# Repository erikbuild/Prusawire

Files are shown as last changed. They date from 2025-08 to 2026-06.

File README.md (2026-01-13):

# Prusawire 2025.B1

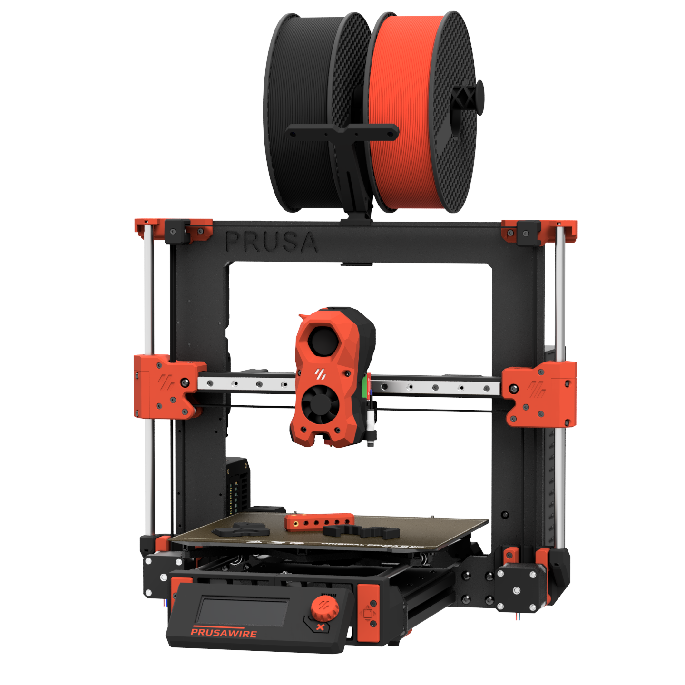
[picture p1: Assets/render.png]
Render


An unofficial Prusa MK3 and MK4 total conversion mod, from Positron's April Fools of 2025.

## Current Release

Beta 1 (2025.B1) was released on 2025-08-21.  There have been [updates and improvements since then](CHANGELOG.md).  Be sure to grab the latest STLs and documentation from the GitHub Repository.

Release 1 (2026.R1) is coming SOON(tm)!

Link to Beta 1 CAD Viewer: [Link](https://positron3d.autodesk360.com/g/shares/SH30dd5QT870c25f12fc28f5f9169dbff2f2)

Link to instructions for gantry de-racking & installing XZ and Y belts: [Link](https://prusawire.positron3d.com/hardware/)

## About

> Nomad of Positron3D came up with this idea shortly after completing their Switchwire build. The idea started as a quick design exercise, to try and convert a Prusa MK4S frame into a Switchwire, using everything left over from a CORE One Upgrade.
>
> As the first iteration wrapped up, I took interest in the project, and decided to take this April Fools joke one step further and build it into a reliable machine.
>
> After months of hard work, please enjoy the build ❤
> 
> -@ellafoxo

## Who This Printer is For

Pick one of the following:

- You have an old MK3, MK3S, or MK3S+, and you want to teach an old dog new tricks and are on a budget
- You upgraded from MK4S to a Core ONE, and have a leftover frame. You are okay spending money on building a new printer with that hardware.

Additionally, the following says this printer is for you: 

- You want to take your first steps into RepRap beyond Prusa, and Voron is an exciting route.
- You are comfortable working from a CAD file as your build guide
- You respect the Frankenstein-y nature of this April Fools joke printer

## Want to Support the Project?

First of all, thank you! Development costs have been mostly self-funded, with filament sponsored by Levendigs, and LDO Motors for providing the funds for the Prusa MK4 frame.

- Support Positron3D to fund future endeavors: 
   - [Donate to Positron3D](https://www.paypal.com/donate/?hosted_button_id=YGPRVTSHN4FQG)
   - [Positron3D Merch](https://nomadsgalaxy-shop.fourthwall.com/)

## Build Volume

X: 250mm
Y: 210mm
Z: 185mm

## Bill of Materials

[Prusawire 2025.B1 Bill of Materials](BOM/BOM_2025-B1.md)

## Technical Support

Prusawire, technically, does not count as a Voron Switchwire. We ask you kindly not to nag the Voron Design team for technical support.

Instead, please [join the Positron3D Discord](https://discord.gg/positron) for support with your build, and maybe share your progress over there too.

## Serial Numbers

We are accepting serials over on the [Positron 3D Discord](https://discord.gg/positron). Please submit your request to the #prusawire-serial-request channel over there. 

## Upgrading the Einsy Rambo to Klipper - Read this

Installing Klipper on the Einsy Rambo board is possible, with extra steps. Follow the guide [published by the awesome folks at MyRigs3D](https://myrigs3d.com/blogs/infos/revive-your-prusa-mk3s-with-klipper-1-5-flash-bootloader)! We recommend Method 2.

**Note:** Some users have reported problems using `avrdude` with the latest Raspberry Pi OS version (bookworm). If you experience error messages from avrdude complaining about gpio ports being busy, please try using the bullseye version of Raspberry Pi OS instead, available as "Raspberry Pi OS (Legacy)" in Raspberry Pi Imager.

## Klipper Configuration Files

The most up–to–date Klipper configuration files for setting up or updating the Prusawire are in our [config repository](https://github.com/Positron3D/prusawire-klipper-config).

## Credits 

Many thanks to all the awesome people and companies that have made this possible. Notably:

Most importantly:
- Ella Fox, _the architect of Beta 1_ - who took Prusawire from a joke to a beautiful and powerful machine. [Buy Ella a Ko-Fi](https://ko-fi.com/ellafoxo)

And also:
- Prusa Research - Cheers, Josef and the team for the MK3/4 platform on which this was built upon!
- Voron Design - Switchwire

- Positron 3D Team - Too many to name, you know who you are <3
- Early development team:
   - Nomad's Galaxy
   - Koosh
   - Birb
- Jason @ LDO Motors - Part sponsorship
- Levendigs - Part sponsorship 
- Early access testers:-
   - Killa_Prints
   - LinksLab
   - Safe
   - Silicon
   - TheNexusAvenger
   - torsten
- Contributors since Beta 1
   - einarjh
   - erikbuild

## Extra Credits for Existing Printed Parts

See the collection for the most up to date! To name them:

- Printable M3 T-Nuts for 3030 Extrusion, by Kapplion
- Stealthburner umbilical strain relief, by nagelwerkstatt

## Team

Prusawire is currently maintained by the Positron 3D Team.

- Design Lead: @Safe-ty
- Documentation Lead: @erikbuild
- Software Lead: @TheNexusAvenger

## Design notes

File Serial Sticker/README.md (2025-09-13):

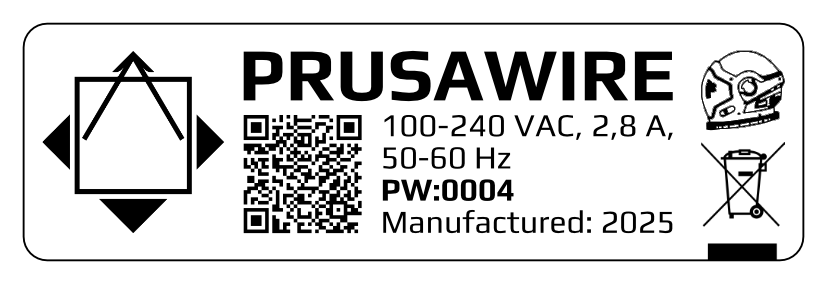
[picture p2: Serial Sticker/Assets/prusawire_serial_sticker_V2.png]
Prusawire Serial


Custom serial sticker for Prusawire. Designed for 24 mm tape. Files include a printable cutting stencil.

Template files are available as Affinity Designer 2 and Inkscape files.
Used fonts are from [Google Fonts](https://fonts.google.com/specimen/Play). Play in regular and bold.

[Inkscape](https://inkscape.org)

[WEEE symbol](https://europa.eu/youreurope/business/product-requirements/labels-markings/weee-label/index_en.htm)

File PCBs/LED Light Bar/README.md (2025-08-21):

# Prusawire Daylight Stick by Ella Fox

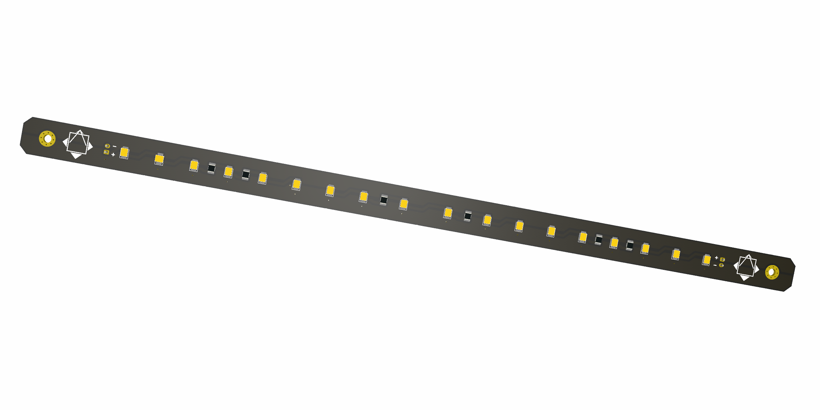
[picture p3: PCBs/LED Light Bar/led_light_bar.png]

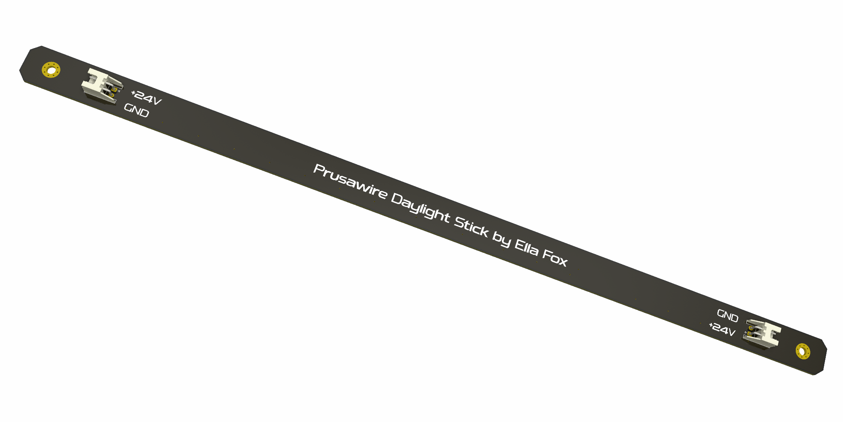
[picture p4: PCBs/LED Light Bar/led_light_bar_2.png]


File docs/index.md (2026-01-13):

---
layout: default
title: Home
nav_order: 1
---

# Positron3D's Prusawire Documentation



An unofficial Prusa MK3 and MK4 to Switchwire total conversion mod, from Positron 3D's April Fools of 2025.

## Current Release

Beta 1 (2025.B1) was released on 2025-08-21.  There have been updates and improvements since then.  Be sure to grab the latest STLs and documentation from the GitHub Repository.

Beta 2 is coming SOON(tm).

## About

> Nomad of Positron3D came up with this idea shortly after completing their Switchwire build. The idea started as a quick design exercise, to try and convert a Prusa MK4S frame into a Switchwire, using everything left over from a CORE One Upgrade.
>
> As the first iteration wrapped up, I took interest in the project, and decided to take this April Fools joke one step further and build it into a reliable machine.
>
> After months of hard work, please enjoy the build ❤
> 
> -@ellafoxo

## Who This Printer is For

Pick one of the following:

- You have an old MK3, MK3S, or MK3S+, and you want to teach an old dog new tricks and are on a budget
- You upgraded from MK4S to a Core ONE, and have a leftover frame. You are okay spending money on building a new printer with that hardware.

Additionally, the following says this printer is for you: 

- You want to take your first steps into RepRap beyond Prusa, and Voron is an exciting route.

## Technical Support

Prusawire, technically, does not count as a Voron Switchwire. We ask you kindly not to nag the Voron Design team for technical support.

Instead, please [join the Positron3D Discord](https://discord.gg/positron) for support with your build, and maybe share your progress over there too.

## Serial Numbers

We are accepting serials over on the [Positron 3D Discord](https://discord.gg/positron). Please submit your request to the #prusawire-serial-request channel over there. 

## Want to Support the Project?

First of all, thank you! Development costs have been mostly self-funded, with filament sponsored by Levendigs, and LDO Motors for providing the funds for the Prusa MK4 frame.

- Support Positron3D to fund future endeavors: 
    - [Donate to Positron3D](https://www.paypal.com/donate/?hosted_button_id=YGPRVTSHN4FQG)
    - [Positron3D Merch](https://nomadsgalaxy-shop.fourthwall.com/)

## Credits 

Many thanks to all the awesome people and companies that have made this possible.

Most importantly:
- Ella Fox, _the architect of Beta 1_ - who took Prusawire from a joke to a beautiful and powerful machine. [Buy Ella a Ko-Fi](https://ko-fi.com/ellafoxo)

And also:
- Prusa Research - Cheers, Josef and the team for the MK3/4 platform on which this was built upon!
- Voron Design - Switchwire
- Positron 3D Team - Too many to name, you know who you are <3
- Early development team:
    - Nomad's Galaxy
    - Koosh
    - Birb
- Jason @ LDO Motors - Part sponsorship
- Levendigs - Part sponsorship 
- Early access testers:
    - Killa_Prints
    - LinksLab
    - Safe
    - Silicon
    - TheNexusAvenger
    - torsten
- Contributors since Beta 1
    - einarjh
    - erikbuild

## Team

Prusawire is currently maintained by the Positron 3D Team.

- Design Lead: @Safe-ty
- Documentation Lead: @erikbuild
- Software Lead: @TheNexusAvenger

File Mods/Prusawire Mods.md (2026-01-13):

# Prusawire Mods

*This is a non-exhaustive collection of Prusawire Mods. Many of these were created for Beta 1.*

## Electronics
- [Prusawire MMU LCD Cover with insert letters by @einarjh](https://www.printables.com/model/1392274-prusawire-mmu-lcd-cover-with-inset-letters)
- [BTT PI TFT50 V2.1 Prusawire Housing by @telefaksi](https://www.printables.com/model/1384689-btt-pi-tft50-v21-prusawire-housing)
- [Prusawire BigTreeTech HDMI 5 Mount by @TheNexusAvenger](https://www.printables.com/model/1377302-prusawire-bigtreetech-hdmi-5-mount)
- [Prusawire ELectronics Tower (w/ xBuddy Box) by @TheNexusAvenger](https://www.printables.com/model/1415732-prusawire-electronics-tower)
- [Prusawire Electronics Tower (w/ all printed parts) by @WaschBaer](https://www.printables.com/model/1464165-skr-mini-e3-v3-printable-case-pi3b-backplate-mods)

## Wiring
- [Prusawire Cable Management Mods by @telefaksi](https://www.printables.com/model/1374187-prusawire-cable-management-mods)
- [Prusawire Cable Management - Additional Mods by @erikbuild](https://www.printables.com/model/1422355-prusawire-cable-management-additional-mods)

## Power Supplies
- [Meanwell LRS-350 / RSP-320 PSU Mount by @erikbuild](https://www.printables.com/model/1386144-meanwell-lrs-350-24-rsp-320-24-psu-mount-for-prusa)

## Decking / Panels
- [Prusawire Deck Panel for Countersunk Screws by @Safe](https://www.printables.com/model/1374282-prusawire-deck-panel-for-countersunk-screws)
- [Prusawire Beta 1 - Rear Deck Cover Plate by @erikbuild](https://www.printables.com/model/1384528-prusawire-rear-deck-cover-plate)

## Frame and Motion
- [Prusawire Key-Bak Mounting Bracket by @telefaksi](https://www.printables.com/model/1371269-prusawire-key-bak-mounting-bracket)
- [TPU Feet for Prusawire and Voron V0 (Alternative to purchased rubber feet!)](https://www.printables.com/model/1442105-tpu-feet-for-prusawire-and-voron-v0)
- [PZ Probe Mount for Prusawire Stealthburner Carriage by @Jarhead](https://www.printables.com/model/1368943-pz-probe-mount-for-prusawire-beta-1)

## Aesthetics
- [Prusawire Supplemental Badge by @TheNexusAvenger](https://www.printables.com/model/1368495-prusawire-supplemental-badge)

## Major Mods
- [XZ Belt Reroute (Under the printer instead of over) by @WaschBaer](https://www.printables.com/model/1466188-beltreroute-better-center-of-mass-more-z-height)

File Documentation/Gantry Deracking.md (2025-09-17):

# Prusawire Gantry Deracking

*This procedure is a composite of initial advice from @ellafoxo, @thenomad, and @safe from the Positron Discord.*

**Current Compatibility:** *Prusawire - Beta 1*

## Overview
The gantry de-racking procedure is critical to ensure smooth motion in X and Z.  The general idea is to loosen certain screws on the gantry, bump the bottom of the gantry against the X and Z motor joints to align, and tighten the screws.

## Prerequisites
- Confirm your frame geometry is square: [Frame Assembly - Geometry Check| Prusa Knowledge Base](https://help.prusa3d.com/guide/2-frame-assembly_427481#427929)
- The following should be assembled already:
	- Frame
	- Z-Axis
	- X-Gantry with toolhead mount
- You should be ready to belt both the X and Z axis.

## Instructions
1. Remove the **toolhead** from the **carriage mount** (if currently installed).
	1. For Stealthburner, see the Stealthburner assembly manual for instructions.
2. Remove the **bed**, **y-carriage**, and **y-rods** completely off the printer (if currently installed).
3. Remove the **bumper block** and **door puller block** from the back of the gantry (if currently installed).

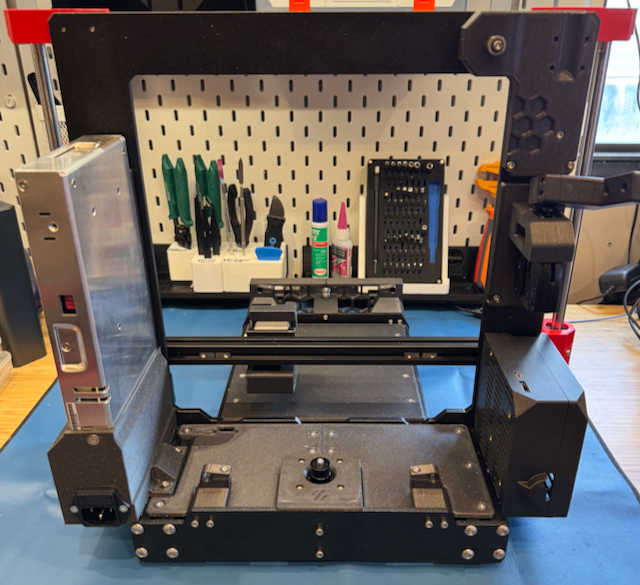
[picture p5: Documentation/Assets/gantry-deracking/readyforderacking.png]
Prusawire ready for deracking.
  	

4. Remove the **top left idler assembly** and **top right idler assembly** loosening the M3 SHCS on each.  
	1. *TIP: A small piece of tape on the top and bottom of the assembly can be used to help keep the bearing stack together.*

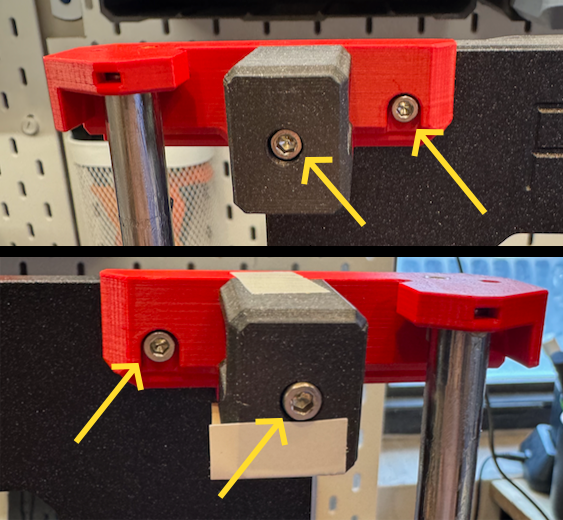
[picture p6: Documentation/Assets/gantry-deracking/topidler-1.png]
Top idlers showing screw locations for removal.
    
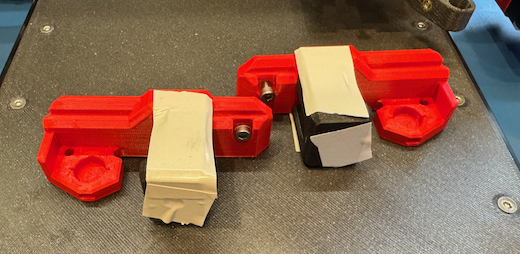
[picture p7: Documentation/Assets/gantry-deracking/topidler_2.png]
Top idles removed and held together with tape.
    

5. Remove the **x-gantry assembly from the printer** by lifting it up off the z-axis rods.
6. Loosen all six **M5 BHCS** from each side of the x-gantry assembly.

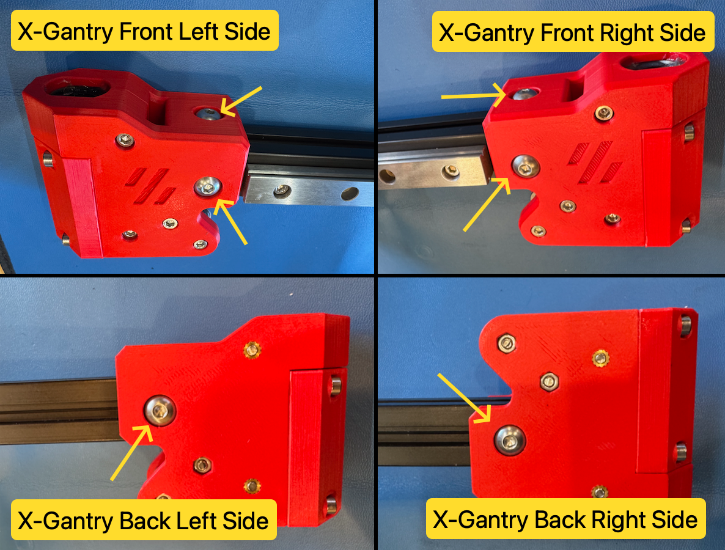
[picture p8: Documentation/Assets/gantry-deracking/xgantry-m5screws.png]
Location of M5 SHCS for adjusting gantry extrusion.
    

7. Ensure each end of the 2020 extrusion is seated ALL the way into the printed parts.
8. Re-install the **x-gantry assembly** onto the printer by sliding it onto the z-axis rods from the top.
9. Move the **x-gantry assembly** up and down a few times to allow parts to settle.
10. Lower the **x-gantry assembly** until it bumps against the X and Z motor mounts.

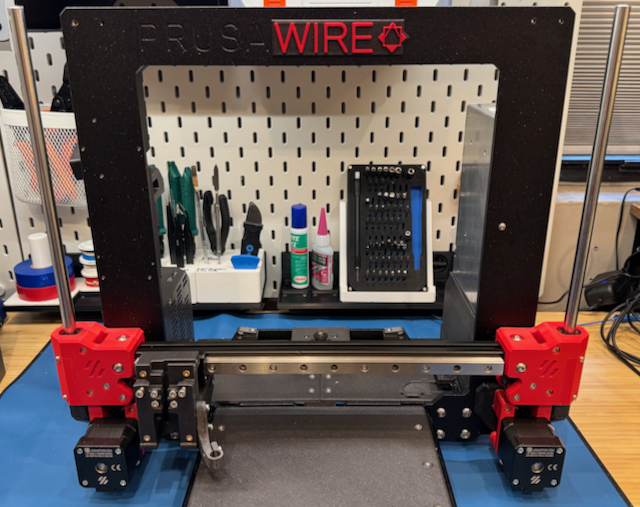
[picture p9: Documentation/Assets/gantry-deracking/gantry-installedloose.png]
Gantry resting on motor mounts.
	

11. Tighten the two top M5 BHCS on the x-gantry assembly, followed by the two front M5 BHCS.

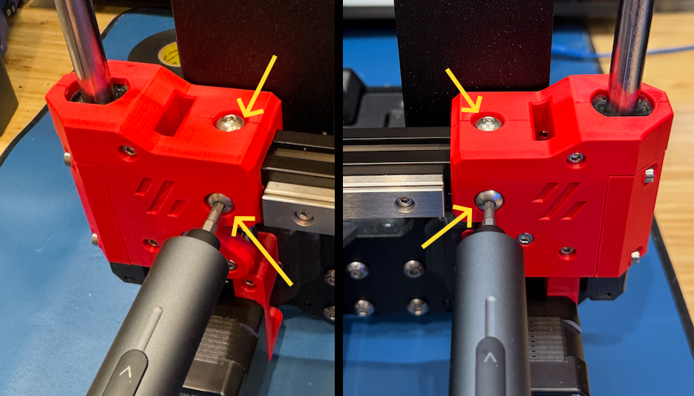
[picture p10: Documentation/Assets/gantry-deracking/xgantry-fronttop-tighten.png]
Image showing M5 BHCS locations.
    

12. Raise the **x-gantry assembly** up to the top just high enough to be able to tighten the rear two M5 BHCS.

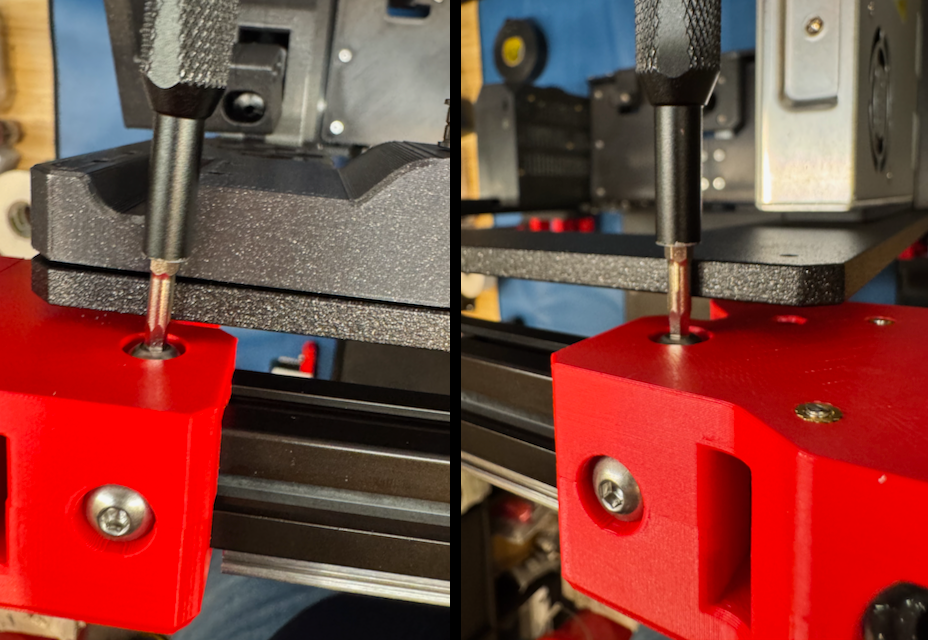
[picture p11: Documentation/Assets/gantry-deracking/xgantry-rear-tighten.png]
Image showing rear M5 BHCS locations on back of gantry.
    

13. Lower the **x-gantry assembly** back down to the bottom.
14. Re-install the **top left idler assembly** and **top right idler assembly** by tightening the two M3 SHCS on each.
15. Re-install the **bumper block** and **door puller block** on the rear of the gantry.
16. Move the gantry up and down.  You shouldn't feel any resistance.

	GIF showing smooth gantry movement and no play.

	1. When the gantry bumps the top of the frame, it should bump equally on both sides.

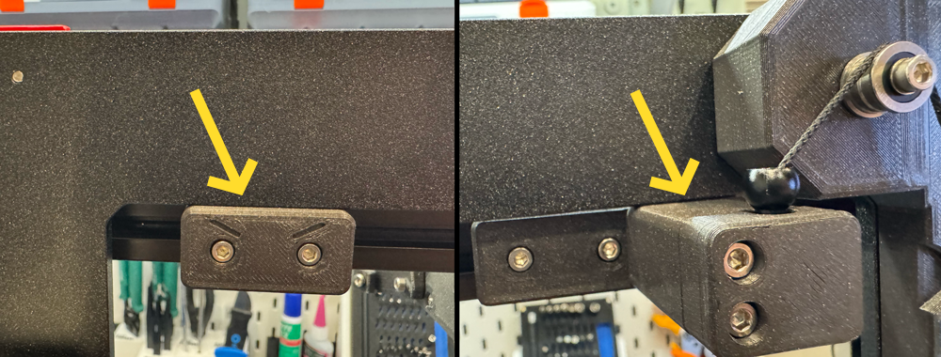
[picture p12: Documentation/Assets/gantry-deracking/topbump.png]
Image showing no gap between bump stop and frame.
    

	2. When the gantry bumps the bottom (X motor mount and Z motor mount), it should bump equally on both sides.

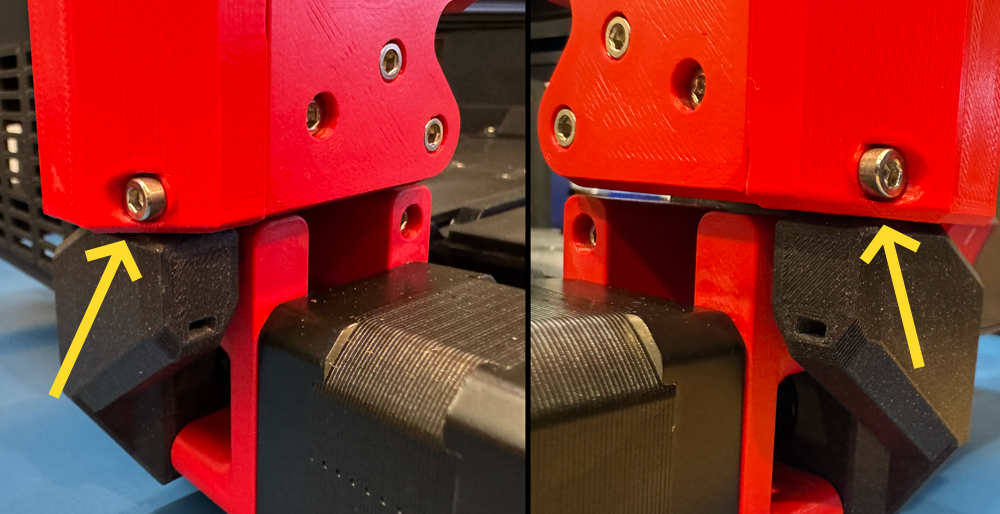
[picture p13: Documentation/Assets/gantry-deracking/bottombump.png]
Image showing no gap between gantry and motor mounts.
    

17. Check for any gantry racking a final time after installing XZ belts (and prior to installation of Y-axis).  Adjust front/top M5 screws if needed.

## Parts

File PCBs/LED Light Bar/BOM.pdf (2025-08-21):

### LED Light Bar

### Page 1

ID | Designator | Footprint | Quantity | Designation Supplier and ref
1 | LED_PLCC_2835_Handsoldering | 18 | LED
2 | R5,R1,R2,R3,R4,R6 | R_1210_3225Metric_Pad1.30x2.65mm_HandSolder | 6 | 100R 0.5W
3 | J1,J2 | JST_XH_S2B-XH-A_1x02_P2.50mm_Horizontal | 2 | Power

D4,D12,D9,D2,D11,D14,D16,D15,D3,
D10,D18,D6,D1,D17,D13,D8,D7,D5

Cree JB2835AWT-W-U40GA0000-N0000001

Digikey: 2138-JB2835AWT-W-U40GA0000-N0000001DKR-ND (https://www.digikey.com/en/products/detail/cree-led/JB2835AWT-W-U40GA0000-N0000001/10820192)

Yageo RC1210JR-07100RL

Digikey: 13-RC1210JR-07100RLDKR-ND (https://www.digikey.com/en/products/detail/yageo/RC1210JR-07100RL/5919841)

JST S2B-XH-A

Digikey: 455-S2B-XH-A-ND (https://www.digikey.com/en/products/detail/jst-sales-america-inc/S2B-XH-A/1651055)

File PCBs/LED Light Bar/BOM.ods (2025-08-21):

ID | Designator | Footprint | Quantity | Designation | Supplier and ref
1 | D4,D12,D9,D2,D11,D14,D16,D15,D3,D10,D18,D6,D1,D17,D13,D8,D7,D5 | LED_PLCC_2835_Handsoldering | 18 | LED | Cree JB2835AWT-W-U40GA0000-N0000001 Digikey: 2138-JB2835AWT-W-U40GA0000-N0000001DKR-ND (https://www.digikey.com/en/products/detail/cree-led/JB2835AWT-W-U40GA0000-N0000001/10820192)
2 | R5,R1,R2,R3,R4,R6 | R_1210_3225Metric_Pad1.30x2.65mm_HandSolder | 6 | 100R 0.5W | Yageo RC1210JR-07100RL Digikey: 13-RC1210JR-07100RLDKR-ND (https://www.digikey.com/en/products/detail/yageo/RC1210JR-07100RL/5919841)
3 | J1,J2 | JST_XH_S2B-XH-A_1x02_P2.50mm_Horizontal | 2 | Power | JST S2B-XH-A Digikey: 455-S2B-XH-A-ND (https://www.digikey.com/en/products/detail/jst-sales-america-inc/S2B-XH-A/1651055)

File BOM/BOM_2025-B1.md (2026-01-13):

# Prusawire 2025.B1 Bill of Materials

This Bill of Materials is accurate for Prusawire version 2025.B1

## Hardware Kit Sources
[KB-3D: BOM Hardware / Fastener Kit - Prusawire - Beta 1](https://kb-3d.com/store/configurators/5743-bom-hardware-fastener-kit-prusawire-beta-1-1755965660392.html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) (affiliate link)

[West3D: Prusawire Stainless Steel Fastener Kit (BDF)](https://collabs.shop/d4usq3) (affiliate link)

| Category | Component | Standard | Optional? | Qty | Notes | Alternative Source 1 | Alternative Source 2 | Alternative Source 3 | Alternative Source 4 |
| --- | --- | --- | --- | --- | --- | --- | --- | --- | --- |
| **Filament** | Primary Color (Black) | PC, ASA, ABS | | 1 | Recommended a carbon or glass filled material to prevent warpage on larger parts. If you cannot print this, then bed adhesive and patience with PC, ABS, or ASA are advised. | [Prusament PC Blend CF (Prusa)](https://www.prusa3d.com/product/prusament-pc-blend-carbon-fiber-black-800g-6)<br>[Affiliate Link](https://www.prusa3d.com/product/prusament-pc-blend-carbon-fiber-black-800g-6/#a_aid=nomad&a_bid=e2885a92) | [FormFutura Kratos PC CF10](https://formfutura.com/product/kratos-pc-cf/)<br><br>[USA (Fabreeko) ASA](https://www.fabreeko.com/products/3do-black-asa-fillament) | [LDO ASA-CF (EU)](https://levendigs.com/collections/filament/products/ldo-asa-cf-filament-1-75mm-1kg-black) | [3DO ASA (EU)](https://3do.dk/en/asa/502-3do-asa-1kg-black.html) |
| | Secondary Color (Red) | | | 1 | | [Prusament ASA (Prusa)](https://www.prusa3d.com/product/prusament-asa-lipstick-red-850g/)<br>[Affiliate Link](https://www.prusa3d.com/product/prusament-asa-lipstick-red-850g/#a_aid=nomad&a_bid=e2885a92) | [Polymaker PolyLite ABS](https://us.polymaker.com/products/polylite-abs?variant=39574342664249) | [LDO ASA (EU)](https://levendigs.com/products/ldo-abs-filament-1-75mm-1kg-red) | [3DO ASA (EU)](https://3do.dk/en/asa/501-814-3do-asa-1kg-red.html#/32-colour-red) |
| **Printed Parts** | Printed Parts | | | 1 | | Print it yourself | Ask a friend | Ask the Positron Discord | |
| **Fasteners** | M5x30 BHCS | ISO 7380 | | 2 | Buy extra fasteners, always! | | | | |
| | M5x16 BHCS | ISO 7380 | | 32  | | | | | |
| | M5x10 BHCS | ISO 7380 | | 4 | | | | | |
| | M5x8 BHCS | ISO 7380 | | 2 | | | | | |
| | M5 Hex Nut | DIN 934 | | 2 | | | | | |
| | M5 T-Nut for 2020 Extrusion | | | 6 | | | | | |
| | M4x10 BHCS | ISO 7380 | | 2 | | | | | |
| | M3x40 SHCS | ISO 4762 / DIN 912 | | 7 | | | | | |
| | M3x30 SHCS | ISO 4762 / DIN 912 | | 22  | Bolt Depot | KB-3D or West3D | Bolt Depot | 3DKatten or TME (EU) | |
| | M3x25 SHCS | ISO 4762 / DIN 912 | | 10  | | | | | |
| | M3x20 SHCS | ISO 4762 / DIN 912 | | 14  | | | | | |
| | M3x16 SHCS | ISO 4762 / DIN 912 | | 7 | | | | | |
| | M3x14 SHCS | ISO 4762 / DIN 912 | | 5 | | | | | |
| | M3x12 SHCS | ISO 4762 / DIN 912 | | 11  | | | | | |
| | M3x10 SHCS | ISO 4762 / DIN 912 | | 82  | | | | | |
| | M3x8 SHCS | ISO 4762 / DIN 912 | | 15  | | | | | |
| | M3x10 BHCS | ISO 7380 | | 11  | Low profile bed cable mount | | | | |
| | M3x30 BHCS | ISO 7380 | | 1 | Used for the Y idler bearing stack. **FYI: 2025 Beta 1 hardware kits from KB-3D and West3D may not yet include this!** | | | | |
| | M3x8 BHCS | ISO 7380 | | 3 | | | | | |
| | M3x6 BHCS | ISO 7380 | Yes | 9 | Used for the newer bed expansion joints. Optional if you use the classic MK3 spacers. | | | | |
| | M3x4 FHCS | ISO 10642 | Yes | 8 | | | | | |
| | M3x16 FHCS | ISO 10642 | Yes | 1 | Used for the MK52 bed in the center. Optional if you use the classic MK3 spacers. | | | | |
| | M3 Shim Washer 3x6x0.5mm | DIN 988 | | 35  | Absolutely do not use normal washers. These must be shim washers built to higher tolerances. | [KB-3D](https://kb-3d.com/store/inserts-fasteners-adhesives/287-3x6x05mm-shim-ring-washer-pack-of-50-din988-1634423217623.html)<br>[Affiliate Link](https://kb-3d.com/store/inserts-fasteners-adhesives/287-3x6x05mm-shim-ring-washer-pack-of-50-din988-1634423217623.html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) | [Replimat Labs (EU)](https://www.replimat.eu/3x6x0.5mm-shim-ring-din-988-40-pcs/rt10079) | [TME (EU)](https://www.tme.eu/de/en/details/b3_6_0.5_bn1976/washers/bossard/1225340/) | [TME (USA)](https://www.tme.com/us/en-us/details/b3_6_0.5_bn1976/washers/bossard/1225340/) |
| | M3 Nylon Lock Nut | DIN 985 | Yes | 7 | 1x needed for y_idler_block. The rest are for Older MK3 Y carriage (if you have the newer MK4 Y carriage, 6x can be eliminated.) | | | | |
| | M3 Hex Nut | DIN 934 | | 10  | 1x needed for y_idler_block. | | | | |
| | M3 Square Nut | DIN 562 | | 14  | Prusa-style M3 Square Nut (Slim) is ideal, but V0 Square Nuts now work! | | | | |
| | M3 Threaded Insert - M3x5x4 (Voron spec) | | | 100 | Buy extra! | [CNC Kitchen (EU)](https://cnckitchen.store/products/made-for-voron-gewindeeinsatz-threaded-insert-m3x5x4-100-stk-pcs) | [Vector3D (UK)](https://vector3d.shop/products/heat-set-insert-m3-voron) | | |
| | M3 T-Nut for 3030 Extrusion | | Yes | 28  | This can be really annoying to source, so we included a printable version instead which uses a heat set insert. Getting the metal ones is totally optional. | [Prusa](https://www.prusa3d.com/product/psu-holder-m3ne-2/)<br>[Affiliate Link](https://www.prusa3d.com/product/psu-holder-m3ne-2/#a_aid=nomad&a_bid=e2885a92) | [KB-3D](https://kb-3d.com/store/extrusion-framing/245-t-nut-roll-in-30-series-8mm-slot-width-m3-threads-1657989315930.html)<br>[[Affiliate Link]](https://kb-3d.com/store/extrusion-framing/245-t-nut-roll-in-30-series-8mm-slot-width-m3-threads-1657989315930.html) | | |
| | M3 T-Nut for 2020 Extrusion | | | 10  | | | | | |
| | M2x10 Self-Tapping Screw for Plastics | | | 4 | Raspberry Pi mounting | | | | |
| **Motion** | GATES GT2 Open Belt LL-2GT-6 (6mm wide) - 1600mm | | | 2 | Genuine GATES belts are required for every open loop belt on the machine. Don't bother with the clones. | [KB-3D](https://kb-3d.com/store/motion/215-gates-powergrip-2gt-belt-open-6mm-width.html)<br>[Affiliate Link](https://kb-3d.com/store/motion/215-gates-powergrip-2gt-belt-open-6mm-width.html?affp=22155) | [West3D](https://west3d.com/products/gates-gt2-open-belt-ll-2gt-6-6mm-wide-voron-v0-v1-v2-switchwire)<br>[Affiliate Link](https://west3d.com/products/gates-gt2-open-belt-ll-2gt-6-6mm-wide-voron-v0-v1-v2-switchwire?dt_id=524416) | [3DKatten (EU)](https://3dkatten.se/products/gates-power-grip-gt-ll-2gt-epdm-balte-1-meter?variant=48182522741059) | |
| | GATES GT2 Open Belt LL-2GT-6 (6mm wide) - 1000mm | | | 1 | [Levendigs (EU)](https://levendigs.com/products/gates-2gt-belt-1cm) | | | | |
| | GT2 20T (6mm wide) Pulley (5mm bore) | | | 3 | | [KB-3D](https://kb-3d.com/store/motion/213-gates-powergrip-2gt-pulley-20-tooth-5mm-6mm-1634481851944.html)<br>[Affiliate Link](https://kb-3d.com/store/motion/213-gates-powergrip-2gt-pulley-20-tooth-5mm-6mm-1634481851944.html?affp=22155) | [West3D](https://west3d.com/products/black-pulleys-and-idlers-gt2-20t-gt2-16t?variant=42151451525332)<br>[Affiliate Link](https://west3d.com/products/black-pulleys-and-idlers-gt2-20t-gt2-16t?variant=42151451525332&dt_id=524416) | [3DKatten (EU)](https://3dkatten.se/products/20t-2gt-5mm-id-pulley?variant=48182169600323) | |
| | F623-2RS Bearing | | | 20  | Don't cheap out here. Use quality bearings for smooth printer operation and longevity. | [KB-3D](https://kb-3d.com/store/magnets-bearings/168-3x10x4-flanged-metric-ball-bearing-f623-2rs-6440891415288.html)<br>[Affiliate Link](https://kb-3d.com/store/magnets-bearings/168-3x10x4-flanged-metric-ball-bearing-f623-2rs-6440891415288.html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) | [West3D](https://west3d.com/products/f623-2rs-flange-ball-bearing)<br>[Affiliate Link](https://west3d.com/products/f623-2rs-flange-ball-bearing?dt_id=524416) | [Replimat (EU [DE])](https://www.replimat.eu/fushi-f623-2rs-abec-7/rt10209) | [AliExpress (Rain & Dew)](https://www.aliexpress.com/item/1005008564381498.html) |
| | Linear Rail MGN12H (300mm), Z1 preload | | | 1 | Z1 preload recommended | [KB-3D](https://kb-3d.com/store/motion/377-5160-kb3d-mgn12h-linear-rail-guide-with-carriage-multiple-lengths-1646161437836.html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)<br>[Affiliate Link](https://kb-3d.com/store/motion/377-5160-kb3d-mgn12h-linear-rail-guide-with-carriage-multiple-lengths-1646161437836.html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) | [West3D](https://west3d.com/products/west3d-printing-mgn12h-1r-300-350-400-linear-rails-with-carriages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)<br>[Affiliate Link](https://west3d.com/products/west3d-printing-mgn12h-1r-300-350-400-linear-rails-with-carriages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) | [3DO (EU)](https://3do.dk/en/linear-rails/1169-1567-ldo-stainless-mgn12h-rail-z1-preload.html#/96-length-300mm) | [Hobby-Store.pl (EU, request length)](https://hobby-store.pl/en/linear-rails/mgn12-linear-rail-400mm-with-mgn12h-carriage.html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) |
| | 8x370mm Linear Rod | | | 2 | X Axis rods, reused for the Y axis | [Prusa](https://www.prusa3d.com/product/smooth-rod-x-axis-mk4-mk3-s-mk2-5-s-mk2-s/)<br>[Affiliate Link](https://www.prusa3d.com/product/smooth-rod-x-axis-mk4-mk3-s-mk2-5-s-mk2-s/#a_aid=nomad&a_bid=e2885a92) | | | |
| | 8x320 or 10x325 Linear Rod | | | 2 | Z Axis rods from MK3/4 | | | | |
| | LM8UU Bearing | | | 3 | | [Prusa](https://www.prusa3d.com/product/linear-bearing-lm8uu/)<br>[Affiliate Link](https://www.prusa3d.com/product/linear-bearing-lm8uu/#a_aid=nomad&a_bid=e2885a92) | [West3D](https://west3d.com/products/lm8uu-smooth-rod-8x15x45-linear-bearing)<br>[Affiliate Link](https://west3d.com/products/lm8uu-smooth-rod-8x15x45-linear-bearing?dt_id=524416) | [Levendigs (EU)](https://levendigs.com/products/myt-lm8uu-linear-bearing-1pc) | [3DO (EU)](https://3do.dk/en/bearings/385-lm8uu.html) |
| | LM10LUU Bearing | | | 2 | These are the Z bearings on MK4. If you are using 8mm rods on Z, replace each 1x LM10LUU with 2x LM8UU instead. | [Prusa](https://www.prusa3d.com/product/linear-bearing-lm10luu/)<br>[Affiliate Link](https://www.prusa3d.com/product/linear-bearing-lm10luu/#a_aid=nomad&a_bid=e2885a92) | | [Levendigs (EU)](https://levendigs.com/products/myt-lm10luu-linear-bearing-1pc) | |
| | Automatic Door Puller, 1kg pull force | | | 1 | This is used in place of a branded Key-Bak, as it is more accessible to purchase outside of the USA.  Remixes for Switchwire spec (*Key-Bak Super48 36in 13oz*) exist as well. | [Amazon (USA)](https://www.amazon.com/dp/B0F2M9GKDT) | [Amazon (Germany)](https://www.amazon.de/dp/B0BRVBHQ1J) | | |
| **Motors (pick one)** | Prusa MK3 X/Y/E Motor | | | 3 | When upgrading directly from MK3, the motors used are as follows:  <br>X motor: X axis (left side)  <br>Y motor: Y axis  <br>E motor: Z axis (right side) | Not recommended for new builds, only converting to Prusawire from old hardware | | | |
| | Prusa MK4 X/Y Motor (plus one additional X or Y motor) | | | 3 | When upgrading directly from MK4, you will need to source one additional Prusa motor since the MK4(S) E motor cannot be used. The motors used are as follows:  <br>X motor: X axis (left side)  <br>Y motor: Y axis  <br>X or Y motor: Z axis (right side) | | | | |
| | LDO 42STH40-1684AC | | | 3 | These steppers are frequently found in Switchwire motor kits. They also sometimes come with the motor required for Stealthburner.  <br>  <br>Use this option when you are building from the leftovers of your Core ONE upgrade kit.<br><br>If using Stealthburner/CW2, consider Switchwire Stepper Kit (with the pancake motor) | [KB-3D](https://kb-3d.com/store/electronics/436-ldo-voron-switchwire-stepper-motor-kit-4-piece-rev-c-1640807333865.html)<br>[Affiliate Link](https://kb-3d.com/store/electronics/436-ldo-voron-switchwire-stepper-motor-kit-4-piece-rev-c-1640807333865.html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) | [onetwo3d (UK)](https://www.onetwo3d.co.uk/product/voron-switchwire-stepper-motor-kit-by-ldo/) | [Blurolls (ships from China)](https://www.blurolls3d.com/products/blurolls-voron-switchwire-3d-printer-motors-kit-made-by-ldo-stepper-motor-kit-3pcs-ldo-42sth40-1684ac-1pc-ldo-36sth20-1004ahg)  | |
| Vibration Management | Rubber Machine Foot 14x11x9mm | | | 4 | | [Replimat Labs (EU)](https://www.replimat.eu/4x-rubber-feet-14x11x9mm-for-v0.2-black/rt10118) | [KB-3D](https://kb-3d.com/store/frame-enclosure/283-rubber-machine-foot-14x11x9mm-set-of-4.html)<br>[Affiliate Link](https://kb-3d.com/store/frame-enclosure/283-rubber-machine-foot-14x11x9mm-set-of-4.html?affp=22155) | [West3D](https://west3d.com/products/14x11x9mm-little-rubber-feet-with-steel-washer)<br>[Affiliate Link](https://west3d.com/products/14x11x9mm-little-rubber-feet-with-steel-washer?dt_id=524416) | |
| **Power Supply (pick one)** | Delta PMZ-24V240WDAL | Prusa Black PSU | | 1 | **The Prusa black PSU is recommended for new builds.**  <br>If you are upcycling an old Prusa with the silver PSU, you can continue to use it. | [Prusa](https://www.prusa3d.com/product/psu-24v-240w-assembly/)<br>[Affiliate Link](https://www.prusa3d.com/product/psu-24v-240w-assembly/#a_aid=nomad&a_bid=e2885a92) | [Printed Solid](https://www.printedsolid.com/products/original-prusa-psu-24v-240w-assembly) | | |
| | PRPZ-24-240 | Prusa Silver PSU | | 1 | Second hand only; only if you have one lying around. | | | | |
| | Meanwell LRS-350-24 | Meanwell PSU | | | Great for USA users, do not use in EU (use RSP-320-24 instead). | [KB-3D](https://kb-3d.com/store/power-supplies-converters/185-meanwell-lrs-350-24-power-supply-24v-350w.html)<br>[Affiliate Link](https://kb-3d.com/store/power-supplies-converters/185-meanwell-lrs-350-24-power-supply-24v-350w.html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) | [West3D](https://west3d.com/products/mean-well-lrs-350-24-150w-24v-6-5a-power-supply-psu)<br>[Affiliate Link](https://west3d.com/products/mean-well-lrs-350-24-150w-24v-6-5a-power-supply-psu?dt_id=524416)<br> | [Digikey](https://www.digikey.com/en/products/detail/mean-well-usa-inc/LRS-350-24/7705034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) | |
| **Mainboard (pick one)** | Einsy RAMBo | | | 1 | | [Prusa](https://www.prusa3d.com/product/einsy-rambo-mk3-s/)<br>[Affiliate Link](https://www.prusa3d.com/product/einsy-rambo-mk3-s/#a_aid=nomad&a_bid=e2885a92) | [Printed Solid](https://www.printedsolid.com/products/original-prusa-einsy-rambo-mk3s) | | |
| | BigTreeTech SKR Mini E3 v3.0 | | | 1 | | [KB-3D](https://kb-3d.com/store/controllers-displays-drivers/420-bigtreetech-skr-mini-e3-v30-32-bit-control-board-1639888431041.html)<br>[Affiliate Link](https://kb-3d.com/store/controllers-displays-drivers/420-bigtreetech-skr-mini-e3-v30-32-bit-control-board-1639888431041.html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) | [West3D](https://west3d.com/products/btt-skr-mini-e3-v3-controller-board-3d-printer-control-system)<br>[Affiliate Link](https://west3d.com/products/btt-skr-mini-e3-v3-controller-board-3d-printer-control-system?dt_id=524416) | | |
| **Frame** | Printer Frame | | | 1 | MK3/S/+ has an older version of this frame. The MK4 version is perforated with hexagons at the rear to reduce weight, and is also a little thicker.  <br>Both versions are absolutely fine for this build. | [Prusa](https://www.prusa3d.com/product/printer-frame/)<br>[Affiliate Link](https://www.prusa3d.com/product/printer-frame/#a_aid=nomad&a_bid=e2885a92) | | | |
| | Front Plate | | | 1 | Stock Prusa MK3 or MK4 | [Prusa](https://www.prusa3d.com/product/front-plate/)<br>[Affiliate Link](https://www.prusa3d.com/product/front-plate/#a_aid=nomad&a_bid=e2885a92) | | | |
| | Rear Plate | | | 1 | | [Prusa](https://www.prusa3d.com/product/rear-plate/)<br>[Affiliate Link](https://www.prusa3d.com/product/rear-plate/#a_aid=nomad&a_bid=e2885a92) | | | |
| | Aluminum Extrusion - Long | | | 2 | | [Prusa](https://www.prusa3d.com/product/aluminum-extrusion-long/)<br>[Affiliate Link](https://www.prusa3d.com/product/aluminum-extrusion-long/#a_aid=nomad&a_bid=e2885a92) | | | |
| | Aluminum Extrusion - Short | | | 2 | | [Prusa](https://www.prusa3d.com/product/aluminum-extrusion-short/)<br>[Affiliate Link](https://www.prusa3d.com/product/aluminum-extrusion-short/#a_aid=nomad&a_bid=e2885a92) | | | |
| | 2020 T-Slot Aluminum Extrusion - 350mm | | | 1 | This is not part of a stock Prusa frame. It will need to be purchased | [Hobby-Store.pl (EU)](https://hobby-store.pl/en/aluminium-profile-2020-type-t-slot/altrax-aluminium-profile-2020-t-slot-type-matt-black.html) | [DLLPDF (Custom length)](https://dllpdf.com/dllpdf-2020-by-the-mm) | [Misumi (USA)](https://us.misumi-ec.com/vona2/detail/110302683830/?HissuCode=HFSB5-2020-350) | [Misumi (EU)](https://de.misumi-ec.com/vona2/detail/110302683830/?HissuCode=HFSB5-2020-350) |
| **Bed Assembly** | Y Carriage | | | 1 | The newer MK4 carriage has perforated hexagonal holes on the bottom to reduce weight.  <br>Both the classic MK3 and the MK4 versions are supported. | [Prusa](https://www.prusa3d.com/product/y-carriage/)<br>[Affiliate Link](https://www.prusa3d.com/product/y-carriage/#a_aid=nomad&a_bid=e2885a92) | [West3D (TriangleLab)](https://west3d.com/products/prusa-mk3-y-carrier-trianglelab)<br>[[Affiliate Link]](https://west3d.com/products/prusa-mk3-y-carrier-trianglelab?dt_id=524416) | [OneTwo3D (LDO) (UK)](https://www.onetwo3d.co.uk/product/ldo-switchwire-y-carriage/) | |
| | Bearing Clips | | | 3 | If you do not have these currently, buy the newer MK4 ones with the rubber spacer, as it makes the bearings slide nicer.  <br>MK3 ones will work fine too. | [Prusa](https://www.prusa3d.com/product/bearing-clips/)<br>[Affiliate Link](https://www.prusa3d.com/product/bearing-clips/#a_aid=nomad&a_bid=e2885a92) | | | |
| | MK52 Heated Bed (24V) | | | 1 | | [Prusa](https://www.prusa3d.com/product/magnetic-heatbed-mk52-24v-assembly/)<br>[Affiliate Link](https://www.prusa3d.com/product/magnetic-heatbed-mk52-24v-assembly/#a_aid=nomad&a_bid=e2885a92) | [KB-3D](https://kb-3d.com/store/heated-bed-electronics/812-ldo-motors-heated-bed-for-switchwire-prusa-mk3-magnetic-24v-1677363868661.html)<br>[Affiliate Link](https://kb-3d.com/store/heated-bed-electronics/812-ldo-motors-heated-bed-for-switchwire-prusa-mk3-magnetic-24v-1677363868661.html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) | [3Dmensionals (EU)](https://www.3dmensionals.de/ldo-24v-magnetic-heatbed-948#attr=9122,13592,9125,9126,23242) | |
| | Expansion Joints (Set) | | | 8 | In place of the newer MK4 spacer and expansion joints, you could continue to use your old spacers from the MK3. | [Prusa](https://www.prusa3d.com/product/expansion-joints-set/)<br>[Affiliate Link](https://www.prusa3d.com/product/expansion-joints-set/#a_aid=nomad&a_bid=e2885a92) | | | |
| | Spacer 3.2x6x8mm | | | 1 | Prusa only sells this as part of MK4S spare parts set. | [McMaster-Carr](https://www.mcmaster.com/92871A011/) | [Prusa](https://www.prusa3d.com/product/spare-parts-mk4s-set/)<br>[Affiliate Link](https://www.prusa3d.com/product/spare-parts-mk4s-set/#a_aid=nomad&a_bid=e2885a92)<br> | [TME (EU)](https://www.tme.eu/en/details/dr336_3.2x8/metal-spacers/dremec/336-3-2x08/) | |
| | Prusa Textured PEI Sheet for MK3/4 Beds | | | 1 | | [Prusa](https://www.prusa3d.com/product/textured-powder-coated-print-sheet/)<br>[Affiliate Link](https://www.prusa3d.com/product/textured-powder-coated-print-sheet/#a_aid=nomad&a_bid=e2885a92) | | | |
| **Electronics** | Hook Up Wire - 15AWG (1.5mm) Stranded Core, Black and Red | | | 8 | | | | | |
| | Raspberry Pi 3B+, 4B+, or Zero 2W | | | 1 | Pi 5 draws a lot of power. We don't recommend it on this build. Alternative to the Pi would be an Orange Pi 4A | | | | |
| | LDO Nitehawk-SB USB Toolhead Board | | Yes | 1 | Super recommended | | | | |
| | Prusa MK3 LCD Screen | | Yes | | MK3 supported. Don't bother if you're starting from MK4 parts | | | | |
| | 5015 Blower Fan, 5V or 24V | | | 1 | Part cooling fan | | | | |
| | 4010 Axial Fan, 5V or 24V, 3 wire (tachometer) | | | 1 | Hotend cooling fan | | | | |
| | LDO Motors Input Shaper Kit | | Yes | 1 | ADXL345 and 5V wiring included for the Raspberry Pi. Super convenient | | | | |
| | 24V to 5V Step Down DC-DC Converter | | Yes | 1 | Internal powering of the Pi. | [KB-3D](https://kb-3d.com/store/power-supplies-converters/259-dc-dc-converter-1224-volt-to-5v-10-amp-50-watt-1648320892173.html) | | | |
| **(Optional) Prusa Silver PSU: Mains wiring** | IEC C14 Fused Inlet, 10A minimum | | Yes | 1 | If using Prusa Silver PSU and Frame Mount | [TME (EU)](https://www.tme.eu/en/details/pf0002_63/iec-60320-connectors/bulgin/) | [electro:kit (EU)](https://www.electrokit.com/en/natbrunn-c14-med-sakringshallare-skruv) | | |
| | ZF Electronics WRG32F2FBRLN | | Yes | 1 | If using Prusa Silver PSU and Frame Mount | [West 3D](https://west3d.com/products/zf-rocker-switch-dpst-16a-on-off-wrg32f2bbrln)<br>[Affiliate Link](https://west3d.com/products/zf-rocker-switch-dpst-16a-on-off-wrg32f2bbrln?dt_id=524416) | [Farnell (EU)](https://de.farnell.com/en-DE/zf-electronics/wrg32f2fbrln/switch-illuminated-rocker-dpst/dp/2136113) | | |
| **(Optional) Meanwell PSU: Mains Wiring** | TycoElectronics - 10EGG1-2 Filtered Power Inlet | | Yes | 1 | If using Meanwell PSU and Frame Mount | [West3D](https://west3d.com/products/tycoelectronics-10ehg1-2-filtered-power-inlet)<br>[Affiliate Link](https://west3d.com/products/tycoelectronics-10ehg1-2-filtered-power-inlet?dt_id=524416)<br> | | | |
| | ZF Electronics WRG32F2FBRLN | | Yes | 1 | If using Prusa Silver PSU and Frame Mount | [West 3D](https://west3d.com/products/zf-rocker-switch-dpst-16a-on-off-wrg32f2bbrln)<br>[Affiliate Link](https://west3d.com/products/zf-rocker-switch-dpst-16a-on-off-wrg32f2bbrln?dt_id=524416) | [Farnell (EU)](https://de.farnell.com/en-DE/zf-electronics/wrg32f2fbrln/switch-illuminated-rocker-dpst/dp/2136113) | | |
| **Cables** | HellermannTyton 170-01000 Helagaine Twist-In Cable Sleeve | 300-350mm length | | 1 | Used to wrap the MK52 bed cables. For MK3, this part is 300mm. MK3.9 and above, this is 350mm. | [Prusa](https://www.prusa3d.com/product/textile-sleeve-35-cm/) | [TME (EU)](https://www.tme.eu/de/en/details/twist-in-05-pet-bk/conduits/hellermanntyton/170-01000/) | [Conrad (EU)](https://www.conrad.com/en/p/hellermanntyton-170-01000-twist-in-05-helagaine-meshwork-hose-black-541298.html) | |
| | HellermannTyton 170-01001 5-8mm Helagaine Twist-In Cable Sleeve | 520mm length | | 1 | Prusa Nextruder cable sleeving. Used for the toolhead | [Prusa](https://www.prusa3d.com/product/textile-sleeve-8x520-mm/) | [TME (EU)](https://www.tme.eu/de/en/details/twist-in-08-pet-bk/conduits/hellermanntyton/170-01001/) | | |
| | 2mm or 3mm Nylon - 555mm | | | 1 | This is the nylon used on Nextruder. It will be used for the Stealthburner wiring.  <br>It can also be used on the heated bed if you don't have your old nylon anymore. If that is the case, by two of them. | [Prusa](https://www.prusa3d.com/product/nylon-3x555-mm/) | | | |
| **Spool Management** | ECAS Bowden Collet 4mm | | Yes | 2 | | | | | |
| | PTFE Tube 4mm OD, 3mm ID, 500mm | | Yes | 1 | Cut to length | | | | |
| | PTFE Tube 4mm OD, 2mm ID, 50mm | | | 1 | For the hotend. Capricorn is suggested if you have it. | | | | |
| | Prusa Spool Holder | | Yes | 1 | Printable version can be used instead | | | | |
| **Z Probe (pick one)** | SuperPINDA | | | 1 | Temp until load cell Z probing. If you are using the older PINDAv2 or v1, we suggest replacing it to improve Z offset stability | | | | |
| | Omron TL-Q5MC2-Z | | | | | | | | |

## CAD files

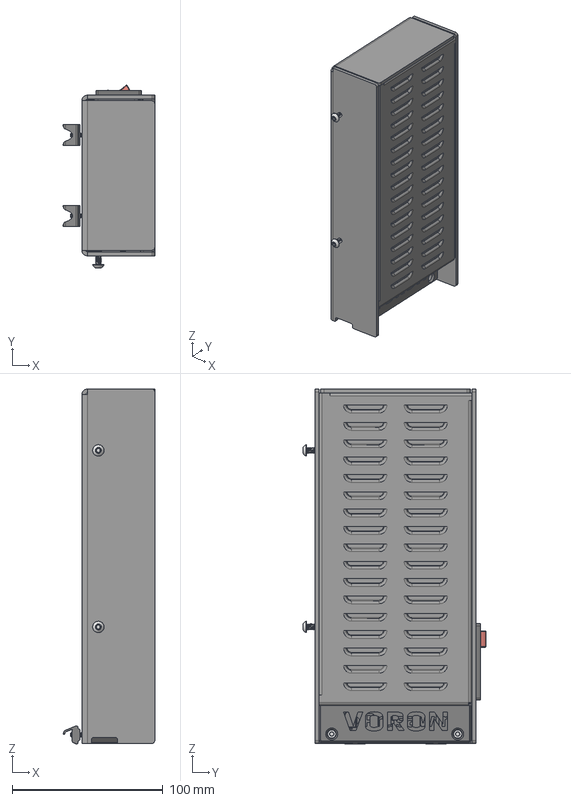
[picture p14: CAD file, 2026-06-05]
CAD/Electronics/PSU Assembly.step
60.7 x 121.2 x 235.3 mm
Switch Housing
Switch
Crimped Spade F
Crimped Spade F (1)
Crimped Spade F (2)
Crimped Spade F (3)
Crimped Spade F (4)
Crimped Spade F (5)
Crimped Spade F (6)
M3x10 SHCS x 4
M4x10 BHCS x 2
DELTA_psu_cover
M3_Hexnut x 2
M3 hex nut T-Nut 3030 x 2
DELTA_psu_cover_1

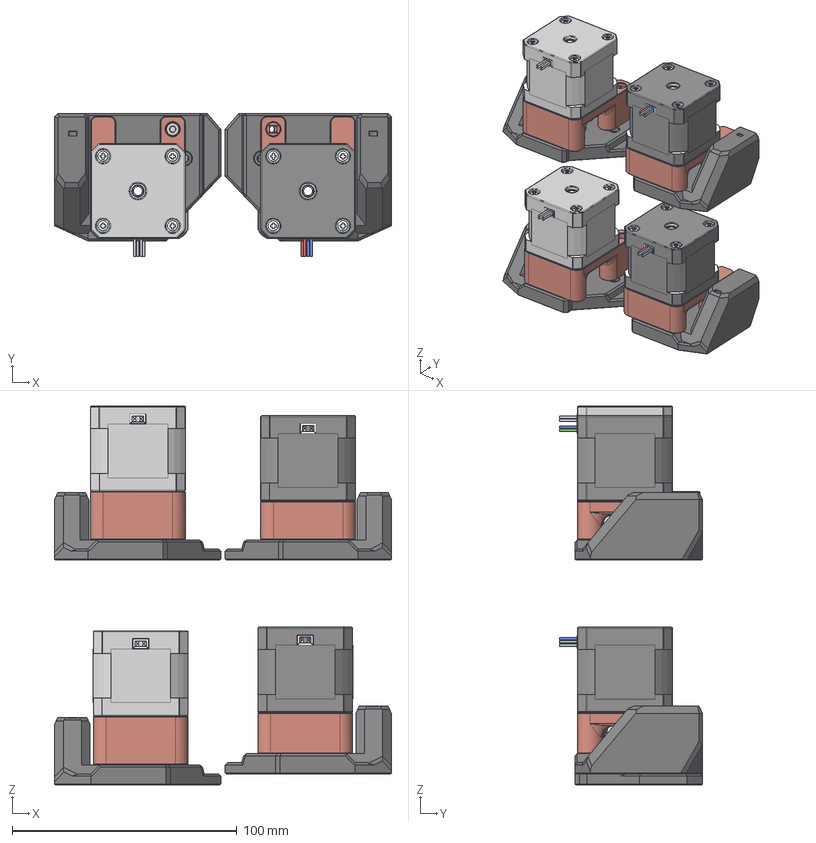
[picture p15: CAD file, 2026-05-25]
CAD/Experimental Files/Double Shear/Standard Motors/Double Shear Assembly.step
150.1 x 63.7 x 168.8 mm
(Unsaved)
M3 Threaded Insert
[a]_motor_mounts_X
X Mount
Grub_screw x 2
Top_Flange
Bottom_Flange
Pulley_Body
M3x20 SHCS x 3
M3x30 SHCS x 2
F695 Bearing
(Unsaved)_1
[a]_motor_mounts_Z
Z Mount
Grub_screw_1 x 2
Top_Flange_1
Bottom_Flange_1
Pulley_Body_1
F695 Bearing_1
(Unsaved)_2
GT2 20T 6MM Pulley
[a]_motor_mounts_Z_1
Z Mount_1
F695 Bearing_2
[a]_motor_mounts_X_1
X Mount_1
(Unsaved)_3
GT2 20T 6MM Pulley_1
F695 Bearing_3

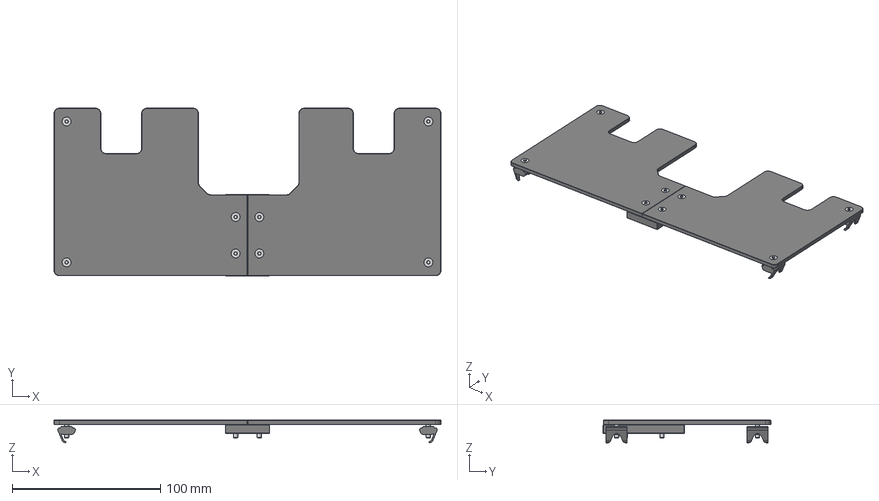
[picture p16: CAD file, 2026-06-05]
CAD/Panels/Rear Panel Assembly.step
261.0 x 113.1 x 15.3 mm
deck_panel_rear_connector
deck_panel_rear_left
M3_Hexnut x 4
M3 hex nut T-Nut 3030 x 4
M3_Hexnut_1 x 4
M3x12 FHCS x 8
deck_panel_rear_right_deltablackpsu

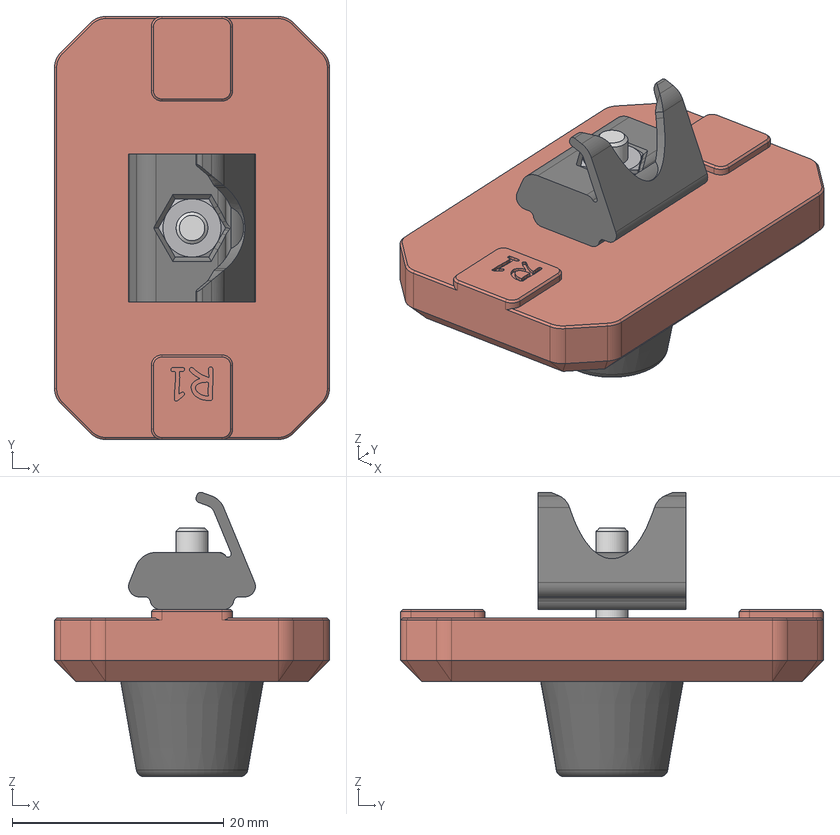
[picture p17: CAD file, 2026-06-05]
CAD/Frame/Feet Assembly.step
26.0 x 40.0 x 26.9 mm
M3x20 SHCS
Rubber Foot - 14x11x9mm
[a]_rubber_foot_block_x4
M3_Hexnut
M3 hex nut T-Nut 3030

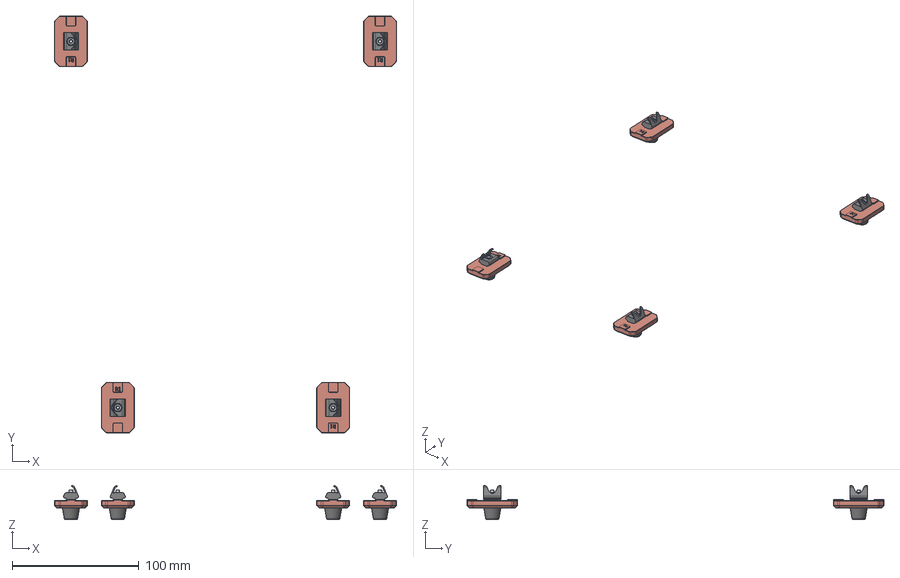
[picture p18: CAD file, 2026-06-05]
CAD/Frame/Feet Assembly (Assembly).step
270.0 x 329.2 x 26.9 mm
M3x20 SHCS x 4
Rubber Foot - 14x11x9mm x 4
[a]_rubber_foot_block_x4 x 4
M3_Hexnut x 4
M3 hex nut T-Nut 3030 x 4

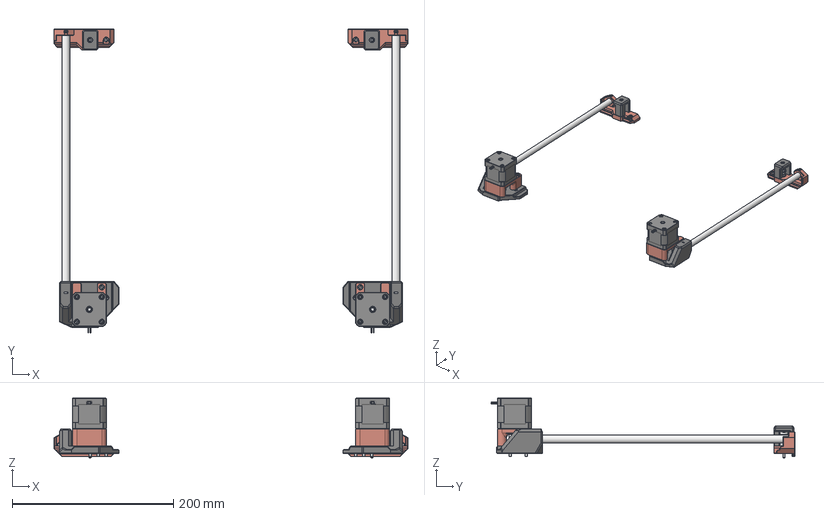
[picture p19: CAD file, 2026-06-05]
CAD/XZ_Axis/XZ Axis Assembly.step
439.6 x 377.2 x 74.1 mm
Linear Rod - 10x325mm x 2
M3 Threaded Insert
z_idler_block_b
Z_Upper_Idlers
M3 Shim 0.5mm x 6mm x 12
F623 Bearing x 8
M3x10 SHCS
M3x30 SHCS_1 x 2
(Unsaved)
Z Mount
Grub_screw x 2
Top_Flange
Bottom_Flange
Pulley_Body
[a]_motor_mounts_Z
M3x10 SHCS_1 x 3
M3x20 SHCS x 3
M3x30 SHCS x 2
M3 Threaded Insert_1
x_idler_block_b
X_Upper_Idlers
M3 Threaded Insert_2
M3x10 SHCS_2
(Unsaved)_1
M3 Threaded Insert_3
[a]_motor_mounts_X
X Mount
Grub_screw_1 x 2
Top_Flange_1
Bottom_Flange_1
Pulley_Body_1
M3x10 SHCS_3 x 3
M3x20 SHCS_1 x 3
M3x30 SHCS_2 x 2

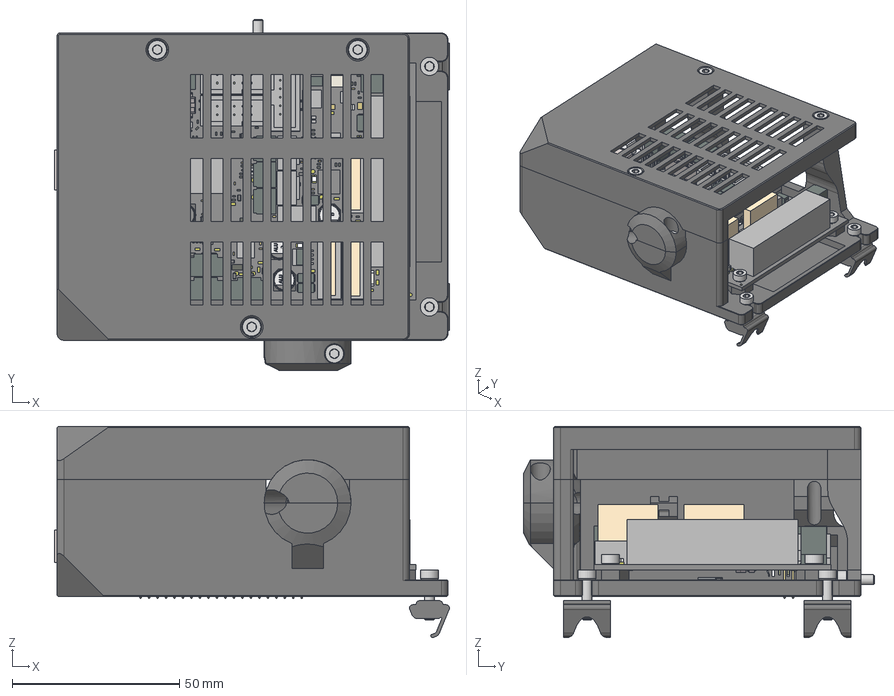
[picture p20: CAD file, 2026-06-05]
CAD/Electronics/Rambo Assembly.step
118.2 x 105.0 x 63.3 mm
PCB
mcu_base_einsy
mcu_cover_einsy
M3 Threaded Insert x 9
M3x10 SHCS x 2
heatbed_cable_clip
M3x20 SHCS x 3
M3x8 SHCS x 5
M3x12 SHCS x 2
M3 hex nut T-Nut 3030 x 2
M3_Hexnut x 2
Board
shield x 2
socket_housing x 2
socket_plate x 2
terminal x 10
HDRV40W64P254_2X20_5080X508X838B
CAPC-0402-T0.55-BN x 49
CAPC-0603-T0.9-BN x 2
INDC-0603 x 2
INDC-0402 x 6
CAPC-0805-T0.95-BN x 7
CAPC-1206-T1.4-BN
RESC-0402 x 14
SRN4018
Micro SD slot
Housing
Shielding
Housing2
Pin1 x 18
Pin2

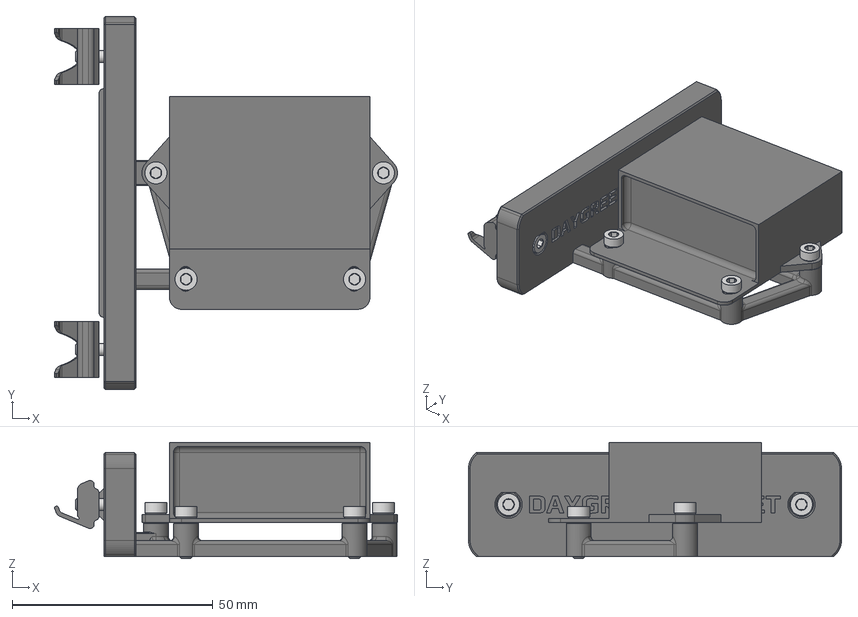
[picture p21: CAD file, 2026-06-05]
CAD/Electronics/Buck Converter Assembly.step
85.5 x 93.0 x 29.0 mm
Daygreen 24V to 5V Converter
daygreen_mosfet_bracket
M3 hex nut T-Nut 3030 x 2
M3_Hexnut x 2
M3x12 SHCS x 2
M3x10 SHCS x 4

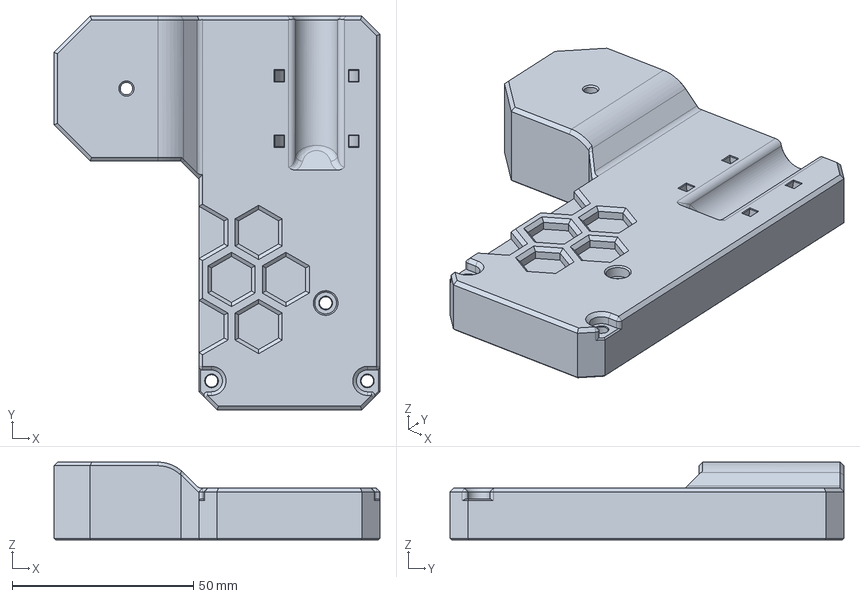
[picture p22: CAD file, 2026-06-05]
CAD/Door_Puller/door_puller_idler_bracket.step
90.0 x 108.7 x 21.5 mm

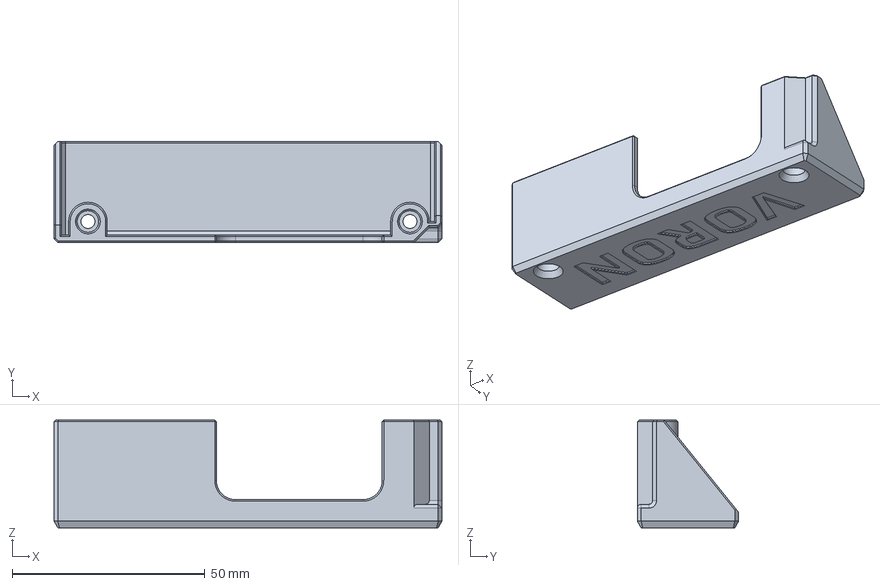
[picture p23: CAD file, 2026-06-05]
CAD/Electronics/Black PSU Covers/black_psu_cover_voron.step
100.6 x 26.3 x 27.9 mm

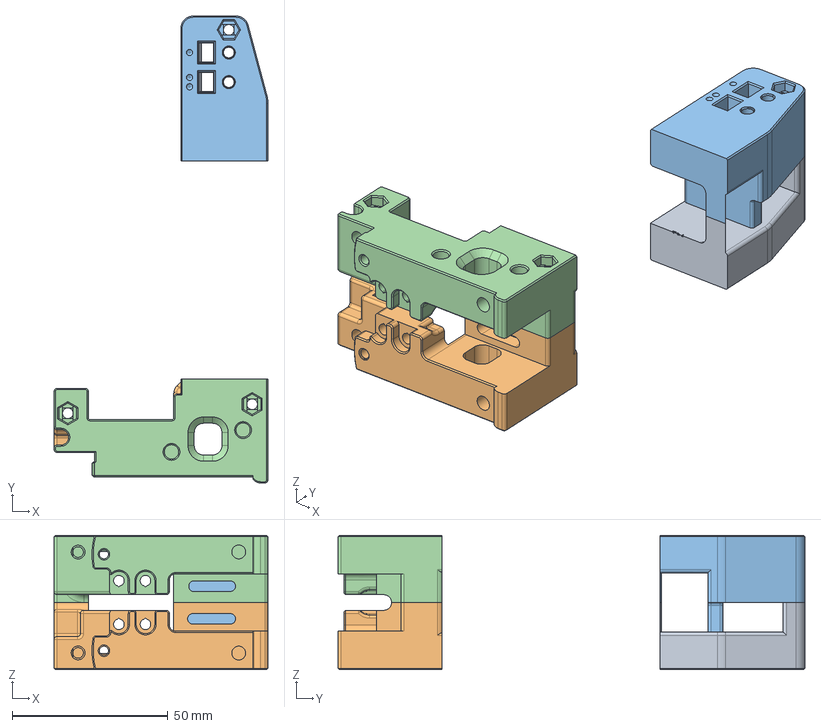
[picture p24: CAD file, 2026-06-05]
CAD/Experimental Files/Belt Attachement Points.step
68.8 x 150.0 x 43.2 mm
x_carriage_left v9
x_carriage_right v12

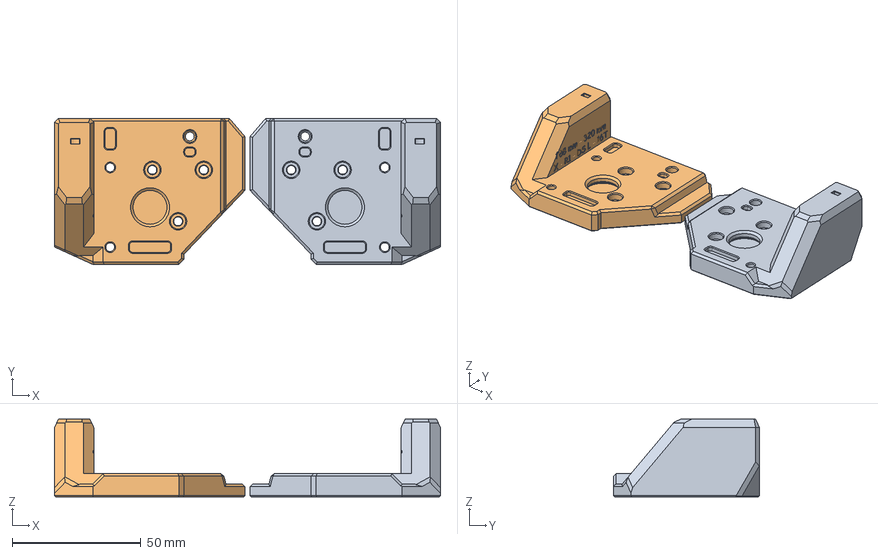
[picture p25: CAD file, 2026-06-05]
CAD/Experimental Files/Double Shear/Long Motor Shafts/STDx8mmx320mmx16T.step
150.1 x 56.8 x 30.1 mm
Z Mount
X Mount (1)

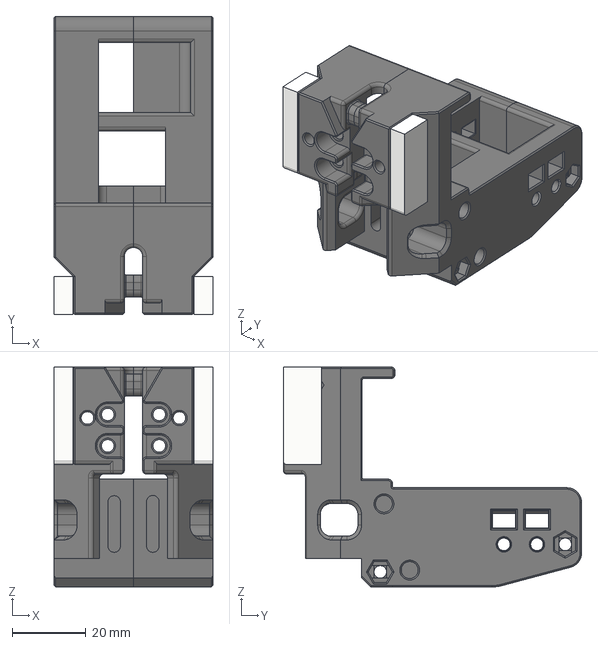
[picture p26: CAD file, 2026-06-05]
CAD/Experimental Files/Expermental Toolheads/x_carriage_db_anthead.step
43.2 x 81.1 x 59.8 mm

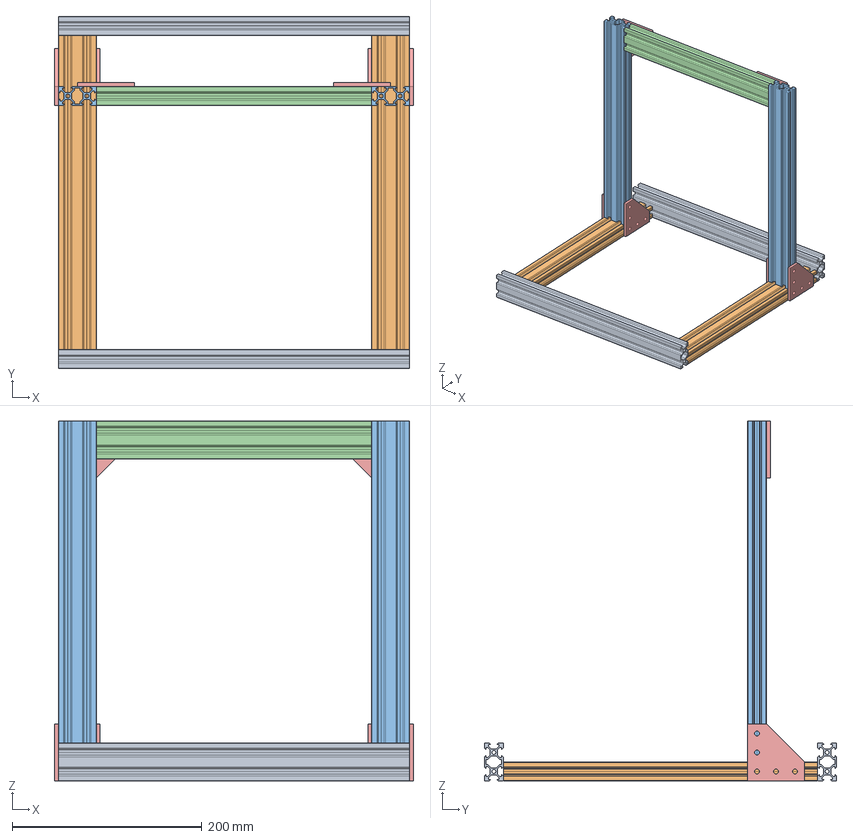
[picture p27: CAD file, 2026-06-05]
CAD/Experimental Files/Prusa Bear Files/Frame and Partial Assembly/Bear Frame.step
378.0 x 371.0 x 379.0 mm
vslot_front_rear x 2
vslot_bottom_sides_mk3 x 2
vslot_vertical_sides_mk3 x 2
vslot_top
Joining Plate 90 Degree.f3d x 6

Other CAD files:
CAD/Experimental Files/Prusa Bear Files/Keyback Parts/door_puller_idler_bracket_bear.step
CAD/Experimental Files/Prusa Bear Files/XZ Bear Parts/[a]_idler_block_a_bear.step
CAD/Experimental Files/Rear Panel Files/deck_panel_rear_left_20T.step
CAD/Experimental Files/Y Front Motors/y_motor_bracket_20T_Pulley_front_mount.step
CAD/Door_Puller/Door Puller Anchor.step
CAD/Door_Puller/Door Puller Idler.step
CAD/Door_Puller/Door Puller.step
CAD/Door_Puller/door_puller_anchor.step
CAD/Door_Puller/door_puller_bracket.step
CAD/Electronics/BTT SB2209 USB Adapter.step
CAD/Electronics/Black PSU Covers/black_psu_cover_prusawire.step
CAD/Electronics/Nitehawk-SB USB.step
CAD/Electronics/Raspberry Pi.step
CAD/Electronics/Wago Mount.step
CAD/Electronics/btt_sb2209_usb_bracket.step
CAD/Electronics/daygreen_mosfet_bracket.step
CAD/Electronics/heatbed_cable_clip.step
CAD/Electronics/mcu_box_einsy.step
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

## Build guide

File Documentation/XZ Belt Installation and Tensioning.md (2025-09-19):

# Prusawire XZ Belt Installation and Tensioning
*This procedure incorporates initial advice from @ellafoxo and others from the Positron Discord.*

**Compatibility:** *Prusawire - Beta 1*

## Overview
The X and Z belts must be installed and tensioned properly to ensure smooth and accurate gantry motion.

**Important notes:**
- Extra belt length has been specified in the BOM; it is expected to have some leftover belt afterwards.
- Match your belt lengths before assembling the printer!
- When inserting the belt clips, there should be an equal number of teeth sticking out of the ends.
- **DO NOT cut your belts** until you are 1000% certain you have done it correctly.  It's okay to leave a little extra length hanging out the back of the toolhead carriage until final assembly and validation.

## Prerequisites
- Complete the Gantry Deracking procedure.
- Remove the **toolhead** from the **carriage mount** (if currently installed).
	1. For Stealthburner, see the Stealthburner assembly manual for instructions.
- (Optional, but highly recommended) Print and assemble the GT2 Belt Runner to easily and perfectly match your belt lengths: [Belt Runner - GT2 Belt Length Matcher \| Printables.com](https://www.printables.com/model/1192440-belt-runner-gt2-belt-length-matcher)

## Instructions 
### Belt Installation
1. Measure out 1600mm of GT2 belt for the X axis.  Double-check your measurement, then cut this length.  Set aside for now.
	- *Tip: Mark some tape on your desk with 100mm increments using a tape measure or calipers.*

    ######

2. Measure out another ~1600mm length of GT2 belt for the Z axis.  **Do not cut it yet!**
3. Match the belt lengths (*note: if not using the GT2 Belt Runner, carefully match the belt lengths by hand!*)
	1. Align the starting teeth of the of the X belt and Z belt.  
	2. Feed into the GT2 Belt Runner (see above).  
	3. Use belt runner to find the exact same length of Z belt as X belt.  Note one belt will be exactly one tooth offset from the other.  
	4. Once you are sure the belts are the same length, cut the **Z belt** to match the **X belt**.

    Belt runner at start and end of belt length.
	
4. Using tape or a zip tie, raise the gantry about 75% of the way towards the top of the frame.

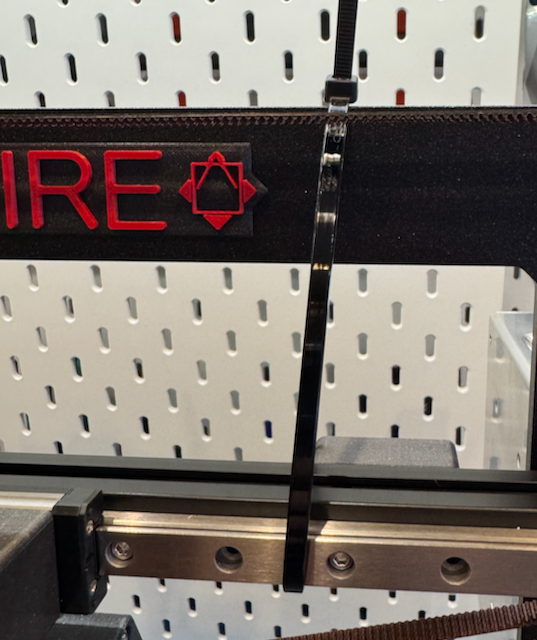
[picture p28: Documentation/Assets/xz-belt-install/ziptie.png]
Zip the gantry most of the way up.
    
	
5. Remove the 4x **M3x14 SHCS** securing the **x carriage assembly** to the linear rail.  Remove the assembly.
	
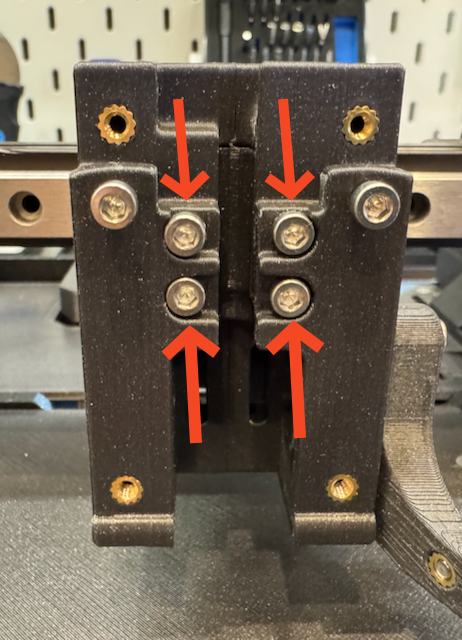
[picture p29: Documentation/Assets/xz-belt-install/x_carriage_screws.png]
Four mounting screws on the front of the x-carriage..
    

6. Remove the 3x **M3x40 SHCS** from the left side of the **x-carriage assembly** to separate the left side from the right side.
	
    Three screws on the left side of the x-carriage.

7. Gather all the needed parts:
	- 2x **1600mm Gates GT2 Belt**
	- 2x **M3x40 SHCS**
	- 2x **\[a]_belt_tensioner_clip**
	- 2x **\[a]_belt_clip**
	- 2x **belt_clip**
	- 4x **M3x14 SHCS**
	- 1x **x-carriage - left side**
	- 1x **x-carriage - right side**

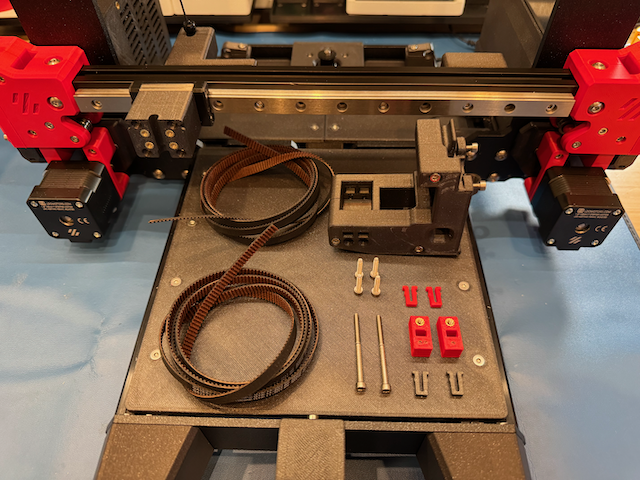
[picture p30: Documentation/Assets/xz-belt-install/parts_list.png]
All needed components shown.
    
    
8. Take the **x-carriage - right side** and install it back onto the **x-carriage mount** (on the rail) with 2x **M3x14 SHCS**.
9. Take the first **\[a]_belt_tensioner_clip**.  Feed a small amount of one of the belts (belt teeth facing up) through the slot on the side with the heat insert.  Pass just enough belt through so 3 teeth are visible from the opposite side.  Insert a **belt_clip** under to secure.
	- *Tip: You can press the retaining clip against a flat surface to help force the retaining clip into the tensioner clip.*
    
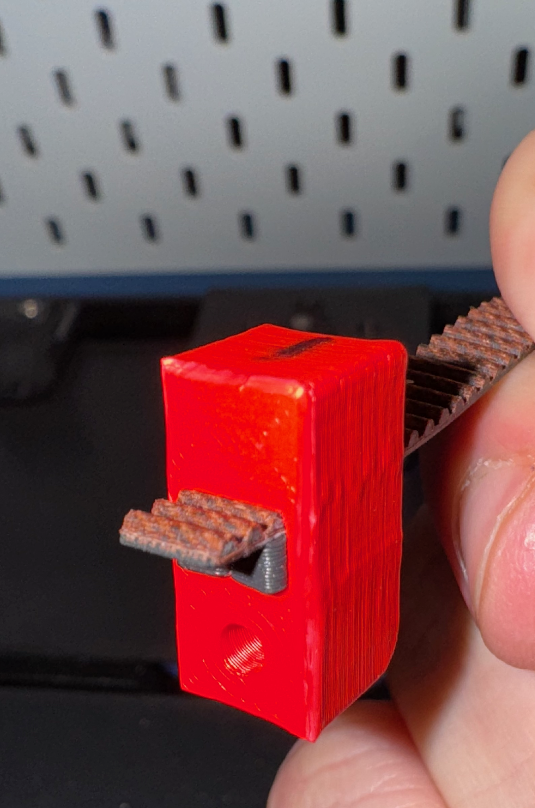
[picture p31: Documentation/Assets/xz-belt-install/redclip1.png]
Image showing no gap between gantry and motor mounts.
    Image showing no gap between gantry and motor mounts.

10. Repeat this process for the other clip and belt.  It is critical for both clips to have the same number of exposed belt teeth showing.
11. Pass the long end of each belt (teeth facing up) through the two slots from the inside to the outside of the mounted **x-carriage - right side**.
	- *NOTE: The **\[a]_belt_tensioner_clip** with the single dot goes towards the rear of the printer.  The clip with the two dots goes towards the front of the printer.

    Image showing no gap between gantry and motor mounts.Image showing no gap between gantry and motor mounts.

12. **Z Belt**: Route the belt through the belt path (see diagram; belt path noted in GREEN):
	1. Right towards the **XZ Block - Right**.
	2. Around the bearing stack and down towards the **Z Motor**.
	3. Back up around the **Z Motor Pulley** through the **XZ Block - Right** towards the **Idler Block - Right**.
	4. Around the bearing stack and left towards **Idler Block - Left**.
	5. Around the bearing stack and down towards **XZ Block - Left**.
	6. Around the bearing stack and right towards the **X-carriage**.
	7. *Tip: Make sure the belt isn't twisted at any point!*
	8. *Tip: Check the Z Motor Pulley alignment with the belt.  Adjust with the set screws on the pulley if needed to ensure good belt alignment that doesn't rub on the motor mounts.*

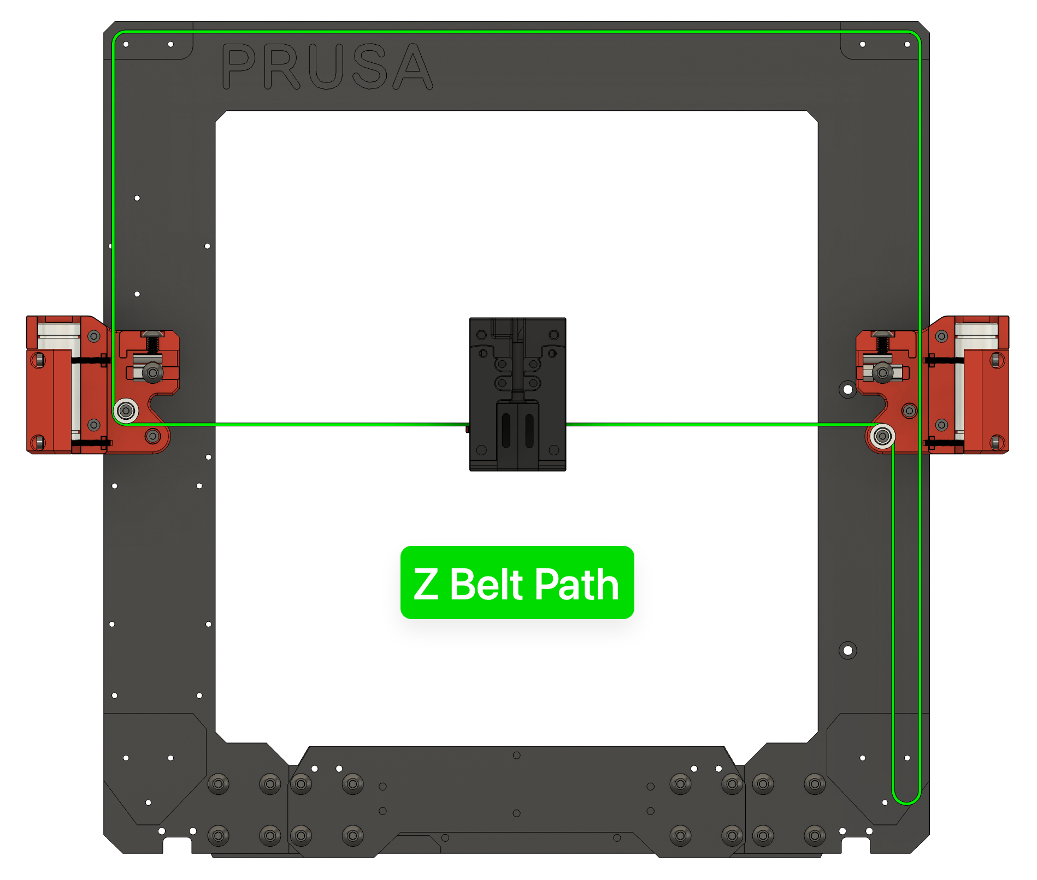
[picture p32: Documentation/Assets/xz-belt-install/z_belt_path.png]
    
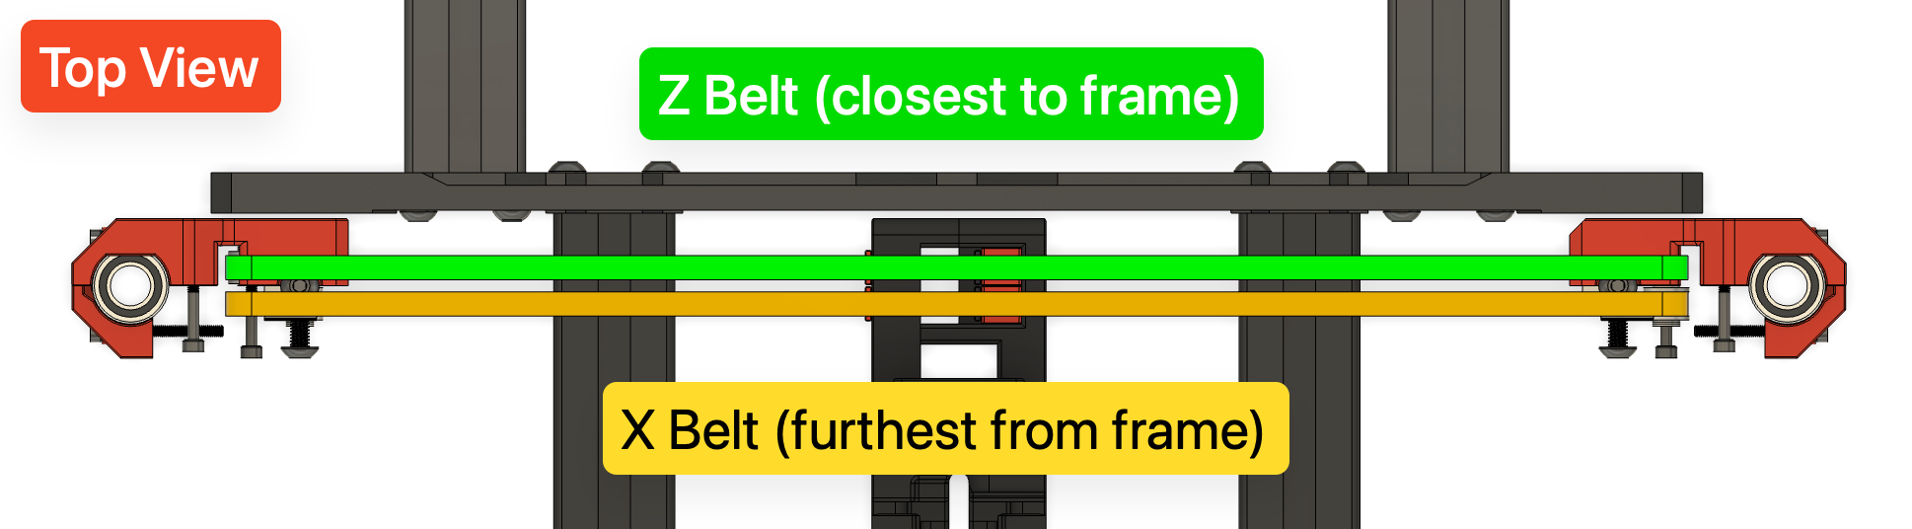
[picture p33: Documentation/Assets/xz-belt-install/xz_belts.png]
    

13. **X Belt**: Route the belt through the belt path (see diagram; belt path noted in YELLOW):
	1. Right towards the **XZ Block - Right**.
	2. Around the bearing stack and up towards **Idler Block - Right**.
	3. Around the bearing stack and left towards **Idler Block - Left**.
	4. Around the bearing stack and down through **XZ Block - Left** towards **X Motor**.
	5. Back up around the **X Motor Pulley** towards **XZ Block - Left**.
	6. Around the bearing block and right towards the **x-carriage**.
	7. *Tip: Make sure the belt isn't twisted at any point!*
	8. *Tip: Check the X Motor Pulley alignment with the belt.  Adjust with the set screws on the pulley if needed to ensure good belt alignment that doesn't rub on the motor mounts.*

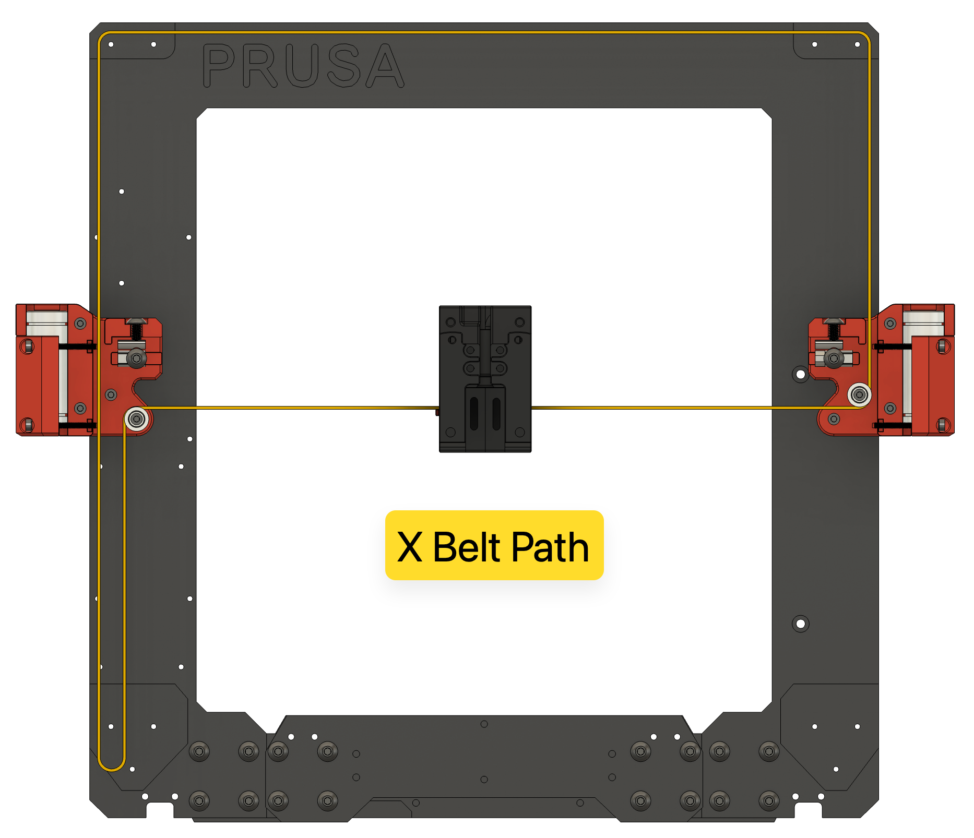
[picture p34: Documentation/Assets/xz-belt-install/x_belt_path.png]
    
	
14. Pass the two belts through the outside of the **x-carriage - left side**.  
	
    

15. Rejoin the **x-carriage - left side** to the mounted carriage with the 3x **M3x40 SHCS**.  Direct the excess belt length down for now.

    

16. Pull the excess belts evenly to remove the slack from the belt system.  Carefully line up the ends of the belts to ensure they are the same length and the ends match up evenly.
17. Insert both **\[a]_belt_clips** to secure the belts to the left side of the carriage.

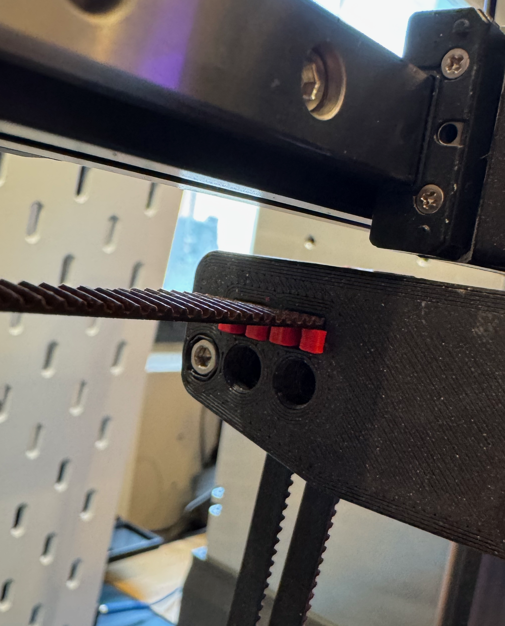
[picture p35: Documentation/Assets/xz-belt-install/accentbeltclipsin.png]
    

18. Confirm once again the ends of the belts are perfectly aligned.  If they have shifted, remove the clips and re-adjust.
19. Unmount the **x-carriage assembly** from the linear rail one last time by removing the 2x **M3x14 SHCS** from the front.
20. Carefully rotate the assembly towards you to view the belts inside.

    

21. Leaving 3 to 4 teeth exposed on the left side of the assembly, carefully cut the belts.

	![[belt-cut.png|300]]

22. Re-mount the assembly back onto the linear rail carriage with all 4x **M3x14 SHCS**.
23. Install the 2x **M3 x 40 SHCS** into the left side of the **x-carriage assembly** and screw into the **\[a]_belt_tensioner_clips** until just seated.
	
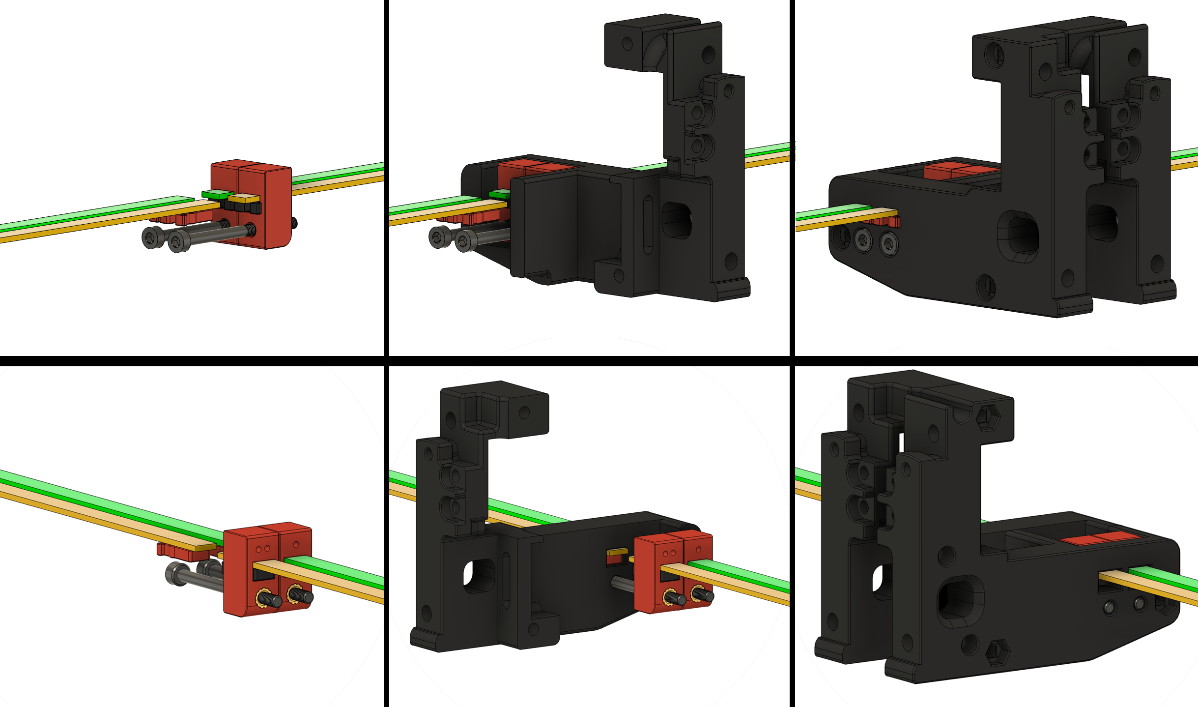
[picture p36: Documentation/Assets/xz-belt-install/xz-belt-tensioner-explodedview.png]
    

24. You are finished and ready to tension the XZ Belts!

    Finished belt assembly.

### Belt Tensioning
To properly tension the X and Z belts:
1. Begin turning the two **M3x40 SHCS tensioning screws** in the **x-carriage assembly**.
	- Turn clockwise to increase tension.
	- Turn counterclockwise to decrease tension.
2. Once slack is removed, and prior to final tension:
	- **TRIPLE CHECK YOUR BELTS to make sure they are riding correctly on the bearings and pulleys.  If they aren't, loosen and correct.**
3. If the tensioning screw bottoms out you can either:
	- Replace the M3x40 SHCS with a fully threaded version
	- Try tensioning both belts a few more groove notches on the left side of the **x-carriage assembly** and re-installing the **\[a]_belt_tensioner_clips** to secure.

4. Visually inspect your X carriage belt tensioner. If your belts are not stretched, you should see that the two tensioner blocks are almost in line with one another. 
	
    
    
5. Come to the front of the printer and inspect the right side of your X carriage. Your belt teeth should align with one another. If they do not, make minor adjustments to the tensioner screws until they do.
	
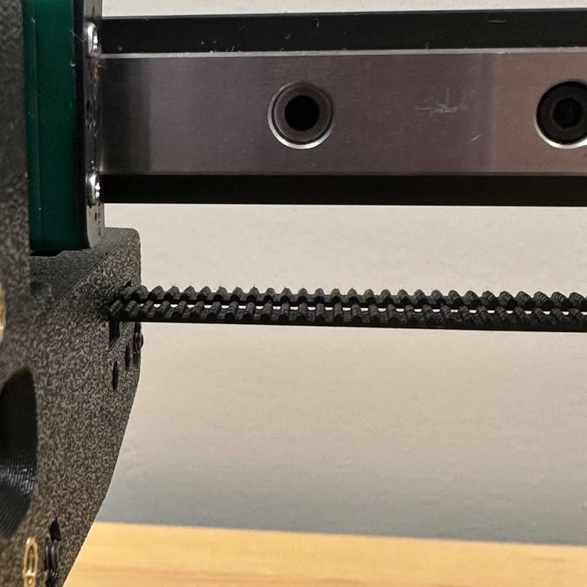
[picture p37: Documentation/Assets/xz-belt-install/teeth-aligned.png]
    

6. Follow up with tuning your belt tension with one of the final tensioning options below.

**Final Tensioning Options:**
- **PF Makes Belt Tensioning Meter:** [3D-Printer/GT2 Belt Tension Meter at main · Diyshift/3D-Printer · GitHub](https://github.com/Diyshift/3D-Printer/tree/main/GT2%20Belt%20Tension%20Meter)
	- Switchwire "Z" Spec - 1.8 to 2.2 (1.9 to 2.3 for EPDM high-temp belt)
- **Prusa Belt Tension Gauge:** [Tension Meter for the GT2 belts of i3 MK3S+ or Prusa MINI+ by Prusament \| Download free STL model \| Printables.com](https://www.printables.com/model/46639-tension-meter-for-the-gt2-belts-of-i3-mk3s-or-prus)
- **Biqu's Digital Belt Tension Tool:** [GitHub - bigtreetech/Belter-belt-tension-Tool: Belter belt tension Tool Info Page](https://github.com/bigtreetech/Belter-belt-tension-Tool)
- **Prusa Mobile App:** 
	- [Prusa on the Apple App Store](https://apps.apple.com/us/app/prusa/id6477531937)
	- [Prusa - Apps on Google Play](https://play.google.com/store/apps/details?id=com.prusa3d.connect&hl=en-US&pli=1)
	- Tuner Mode for *MK3S --> X-Axis*
		- Carriage all the way to the right
- **Prusa Website Tuner:** [Prusa Belt tuner](https://belt.connect.prusa3d.com/)
	- *MK3S --> X-Axis*
		- Carriage all the way to the right
- **Gates Carbon Drive Mobile App**
	- [Carbon Drive Belt Tension Tool on the Apple App Store](https://apps.apple.com/app/bicycle-belt-tension-meter/id438346486)
	- [Carbon Drive - Apps on Google Play](https://play.google.com/store/apps/details?id=com.gates.carbondrivecalculator&hl=en)
	- 85 Hz

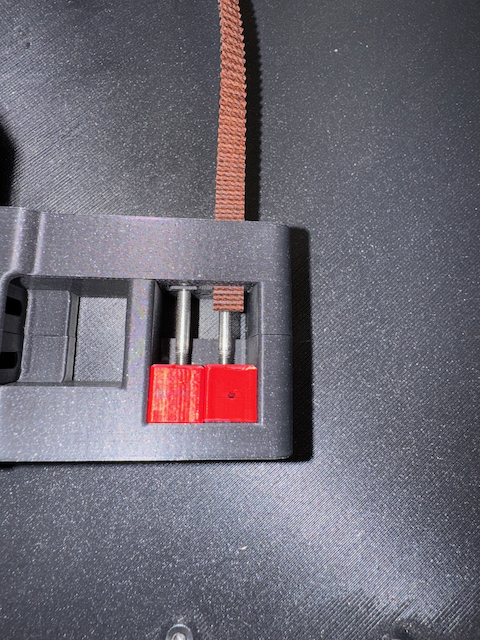
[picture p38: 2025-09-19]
Documentation/Assets/xz-belt-install/z_belt_teeth.png

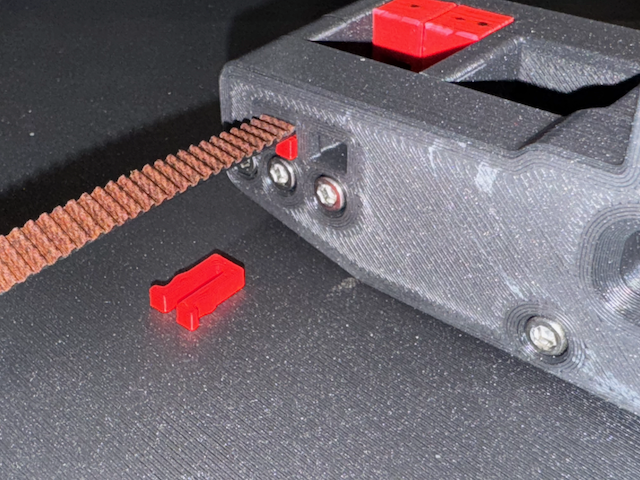
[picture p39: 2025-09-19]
Documentation/Assets/xz-belt-install/zbelt_accent_clip_installation.png

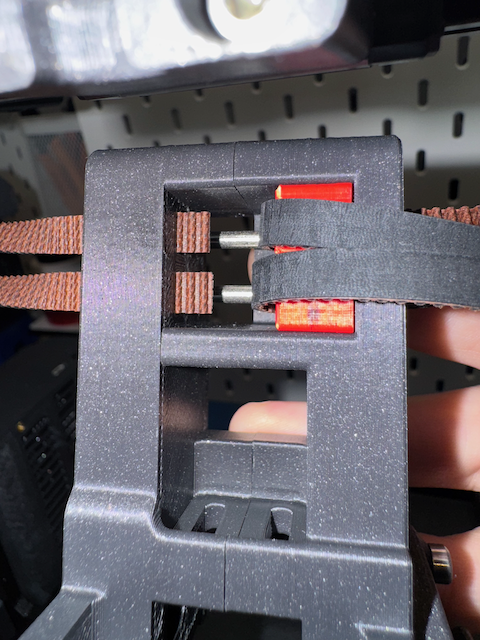
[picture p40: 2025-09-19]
Documentation/Assets/xz-belt-install/belt_matching_teeth.png

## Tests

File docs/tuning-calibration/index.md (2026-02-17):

---
layout: default
title: Tuning and Calibration Overview
has_children: true
nav_order: 8
---

# Tuning and Calibration Overview
{: .no_toc}

<details open markdown="block">
  <summary>
    Table of contents
  </summary>
  {: .text-delta }
- TOC
{:toc}
</details>

## General Resources
- The best tuning resource there is: [Ellis' Print Tuning Guide](https://ellis3dp.com/Print-Tuning-Guide/articles/index_tuning.html)
- Minimal 3DP's Basic Klipper Configuration Checks Procedure
	- [Klipper Basic Configuration Checks - Google Sheets](https://docs.google.com/spreadsheets/d/1CwccwL21RJTX0NQu1DDUu3yGtK1RVByJQGIV45AjyNA/edit?gid=0#gid=0)
- OrcaSlicer's Calibration Info: [Calibration · SoftFever/OrcaSlicer Wiki · GitHub](https://github.com/SoftFever/OrcaSlicer/wiki/Calibration)

Prioritize the following items, IN ORDER:
 1. [Extruder Calibration](https://ellis3dp.com/Print-Tuning-Guide/articles/extruder_calibration.html) (*100mm requested = 100mm extruded*)
 2. Bed Leveling / Bed Mesh (*this will vary depending on your chosen sensor*)
 3. [First Layer Squish](https://ellis3dp.com/Print-Tuning-Guide/articles/first_layer_squish.html)
 4. [Pressure Advance](https://ellis3dp.com/Print-Tuning-Guide/articles/pressure_linear_advance/introduction.html)
	Use the [Pattern Method](https://ellis3dp.com/Print-Tuning-Guide/articles/pressure_linear_advance/pattern_method.html) via [OrcaSlicer's Built-in Calibration Tools](https://github.com/OrcaSlicer/OrcaSlicer/wiki/pressure-advance-calib)
 5. [Extrusion Multipler](https://ellis3dp.com/Print-Tuning-Guide/articles/extrusion_multiplier.html)
 6. [Flow Rate (YOLO method is recommended)](https://github.com/OrcaSlicer/OrcaSlicer/wiki/flow-rate-calib)
 7. [Retraction](https://github.com/OrcaSlicer/OrcaSlicer/wiki/retraction-calib)
 8. [Cornering](https://github.com/OrcaSlicer/OrcaSlicer/wiki/cornering-calib)

- Minimal 3DP's Klipper Calibrations Spreadsheet (*this can be useful for helping calculate much of the above*)
	- [Klipper Calibrations - Google Sheets](https://docs.google.com/spreadsheets/d/1LlSHsa86RuT_btswmDsmQp0LrTJ9U0HJcRhorsqz1ug/edit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)
		- Run Current
			- *particularly if using the BTT SKR Mini E3 V3.0 which can handle higher currents than the Einsey RAMbo...*

## Input Shaping
There's too much here to exhaustively detail, but you'll need an input shaper sensor (ADXL etc) which you may or may not have on your toolhead.  Remember, Prusawire is a bed slinger and you will want to input shape Y axis as well!  The on-toolhead sensors will not detect Y axis.

[Klipper Shake&Tune](https://github.com/Frix-x/klippain-shaketune) works well.

## Skew / Scaling Correction
Some filament shrinks noticably (ABS/ASA espesically).  Prusawire and Voron-adjacent printers are designed with ABS shrinkage in mind and require no scaling.  Not all projects do this!

[Califlower MK2](https://vector3d.shop/products/califlower-calibration-tool-mk2) is an excellent tool to compensate for material shrinkage AND skew.  It is, however, a paid model.

A great free/open source option is Calistar: [Printables](https://www.printables.com/model/778188-calistar-parametric-open-source-alternative-to-cal) and [GitHub](https://github.com/dirtdigger/fleur_de_cali).

## Miscellaneous Notes
- Ella suggests that if using SKR Mini, motor currents can increase over the values provided for the slower Rambo board.  See Run Current above.

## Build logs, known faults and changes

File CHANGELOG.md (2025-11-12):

# Prusawire Change Log

Updated periodically to note significant design changes, fixes, and enhancements.

- 2025-11-15
    - Update y_belt_tensioner_front to allow recessed screw cap head.  Update tensioner screw to M3x16 SHCS in BOM.  Update y_belt_tensioner_rear to have M3S and V0SN variants. (via @erikbuild)
- 2025-11-05
    - Documentation site launched ([https://positron3d.github.io/Prusawire](https://positron3d.github.io/Prusawire)) (via @erikbuild)
- 2025-10-31
    - Update XZ Blocks to have a variant for Prusa-style slim M3 Square Nuts as well as V0-style M3 Square Nuts. (via @Safe-ty)
    - Update Upper Idler Blocks to increase tolerance band for Z-rod lengths. (via @Safe-ty)
- 2025-10-11
    - y_idler_bracket replaced / updated with much stronger version. (via @erikbuild)
    - Added Rod Length Compatibility to motor mounts and idler brackets (via @Safe-ty)
        - Support 8mm rods: 320, 325, and 330mm lengths
        - Support 10mm rods: 320, 325, 330, and 341 lengths
        - Changed file structure to sort motor mounts by diameter
- 2025-10-07
    - Support for V0 Square Nuts for XZ Blocks, Y-Axis Parts (via @Safe-ty)
- 2025-10-06
    - Increase tolerance for 2020 Extrusion Length in XZ Blocks (via @Safe-ty)
        - Allow for 350 +2.0mm length
- 2025-08-26
    - Update idler blocks to eliminate belt rubbing (via @Ellafoxo)
- 2025-08-21
    - 2025.B1 "Beta 1" Released! (via @Ellafoxo)

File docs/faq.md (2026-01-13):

---
layout: default
title: "FAQ"
nav_order: 3
---

# Frequently Asked Questions

## Where is the latest BOM (Bill of Materials)?

The latest BOM can be [found on GitHub in the BOM folder](https://github.com/Positron3D/Prusawire/tree/main/BOM).

## How can I get a Serial # for my finished build?

We are accepting serials over on the [Positron 3D Discord](https://discord.gg/positron). Please submit your request to the `#prusawire-serial-request` channel over there.  There is an example submission and numerous other builds to reference for the format.

## Where can I get help with my build?

The community over on the [Positron 3D Discord](https://discord.gg/positron) is very helpful.  Check out the `#prusawire-questions` channel there.

## The M3 T-Nut for 3030 Extrusion are expensive // What is the recommended Printed Replacement?
The cost of actual roll-in T-Nuts for 3030 Extrusion really isn't worth it.  We suggest this excellent printed model which uses the same M3 Heat Set Inserts.

[Printable M3 T-Nuts for 3030 Extrusion, by Kapplion](https://www.printables.com/model/720045-printable-m3-t-nut-for-3030-extrusion-prusa-xl)

## My Y-Carriage (using the older U-Bolt Bearing Clips) is hitting the front idler!

This is a known issue.  The newer MK4 style bearing clips have a rubber and plastic spacer that sits between the Y-Carriage and the bearing which raises it ~1-2mm up and provides the clearance. 

We are actively investigating a workaround for users of the U-Bolts and will update shortly!

## How do I make the cool silver serial sticker once I have my serial#?

Instructions from @Telefaksi (PW.0004):
>Custom serial sticker for Prusawire. Made for 24 mm tape, I used Brother TZe-M951 Black/Matt Silver tape. Included are Affinity Designer 2 package folder as .zip, .stl and .step files for printable cutting stencil. QR-code is made with Affinity Designer's QR-code tool so url can be edited to link to your serial request post. I exported .png image and imported it to Brother's P-touch Editor for printing.  
>Fonts are included in the package but in case you want to download them the fonts are from Google fonts. Play in regular and bold. https://fonts.google.com/specimen/Play
>In images folder is WEEE marking as vector image.

## My NiteHawk-SB loses connection when there is a restart

If you are running V1.5 of the LDO Motors NiteHawh-SB USB board (the board that connects to the Raspberry Pi): you need to remove BOTH R6 and R7.

> the issue on NH-SB with a 1.5 USB board that looses communication after a "firmware restart" and needs a power cycle to turn back on is caused by the R7 and R6 resistor. They both need to be removed. There is a guide and video that shows how to remove the R7 here its the same for R6. If you are unable to or damage while trying reach out to your reseller where the kit was purchased and they will send you a replacement.
> @JoseFromLDO on the Voron Discord

[PDF Instruction Guide](assets/NiteHawkSB_R6-R7_Resistor_Removal_Guide.pdf): this details for R7, but you will ALSO need to remove R6!



## The Raspberry Pi is having trouble connecting to the controlboard after restarts

This is a common issue.  See https://www.answeroverflow.com/m/1061111415471079444

TL;DR remove modemmanager if you're using MainsailOS.

```sudo apt remove modemmanger```

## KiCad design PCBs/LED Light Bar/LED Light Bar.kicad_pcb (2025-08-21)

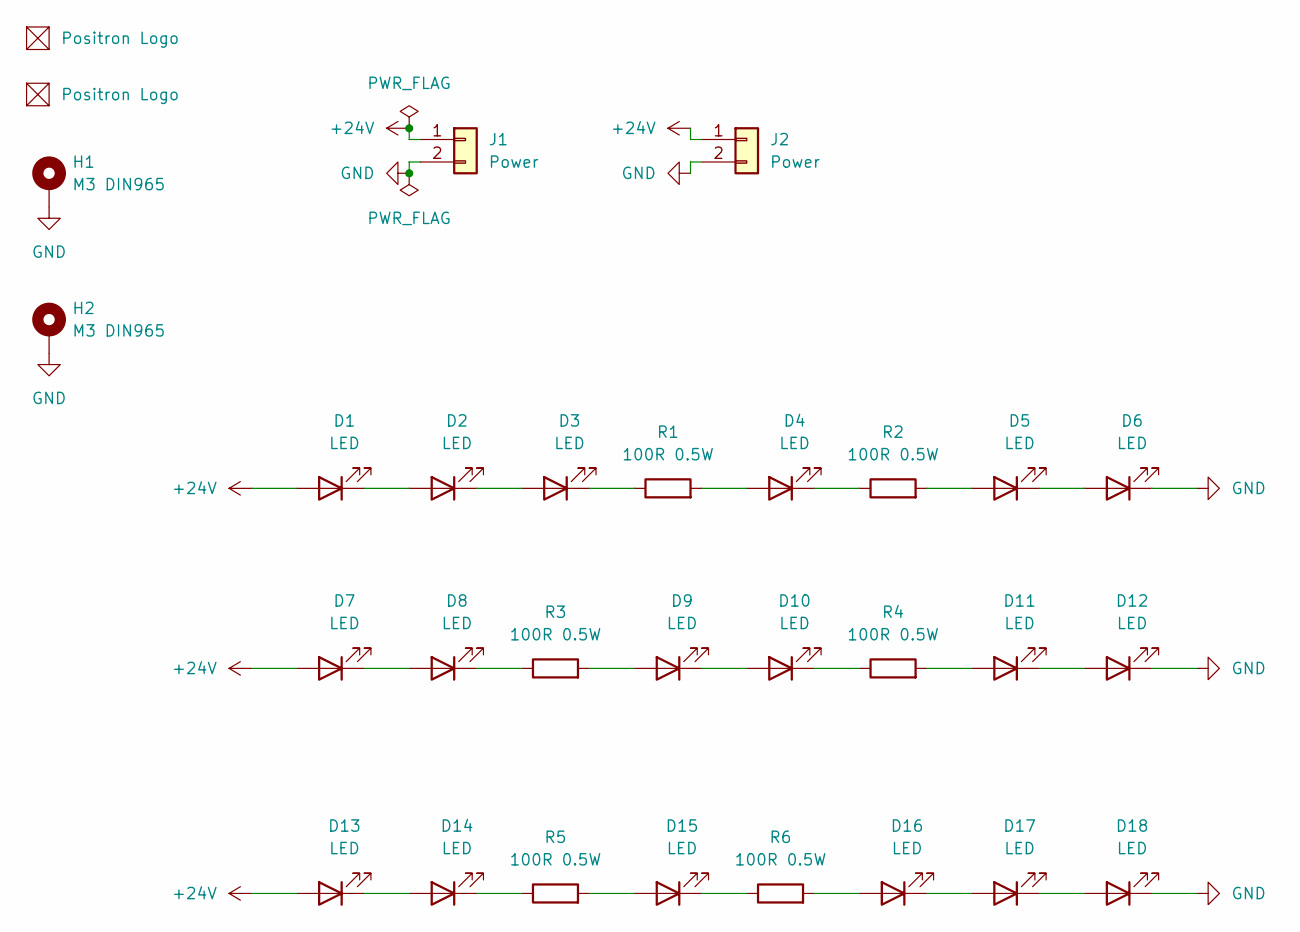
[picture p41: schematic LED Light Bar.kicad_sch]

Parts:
D1, D2, D3, D4, D5, D6, D7, D8, D9, D10, D11, D12, D13, D14, D15, D16, D17, D18: LED; LED_PLCC_2835_Handsoldering; LCSC C182223
H1, H2: M3 DIN965; MountingHole_3.2mm_M3_Pad_Via
J1, J2: Power; JST_XH_S2B-XH-A_1x02_P2.50mm_Horizontal
R1, R2, R3, R4, R5, R6: 100R 0.5W; R_1210_3225Metric_Pad1.30x2.65mm_HandSolder; LCSC C137089
S1, S2: Positron_Logo

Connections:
+24V: D1.2 (A), D7.2 (A), D13.2 (A), J1.1, J2.1
GND: D6.1 (K), D12.1 (K), D18.1 (K), H1.1, H2.1, J1.2, J2.2
unnamed: D1.1 (K), D2.2 (A)
unnamed: D2.1 (K), D3.2 (A)
unnamed: D3.1 (K), R1.1
unnamed: D4.2 (A), R1.2
unnamed: D4.1 (K), R2.1
unnamed: D5.2 (A), R2.2
unnamed: D5.1 (K), D6.2 (A)
unnamed: D7.1 (K), D8.2 (A)
unnamed: D8.1 (K), R3.1
unnamed: D9.2 (A), R3.2
unnamed: D9.1 (K), D10.2 (A)
unnamed: D10.1 (K), R4.1
unnamed: D11.2 (A), R4.2
unnamed: D11.1 (K), D12.2 (A)
unnamed: D13.1 (K), D14.2 (A)
unnamed: D14.1 (K), R5.1
unnamed: D15.2 (A), R5.2
unnamed: D15.1 (K), R6.1
unnamed: D16.2 (A), R6.2
unnamed: D16.1 (K), D17.2 (A)
unnamed: D17.1 (K), D18.2 (A)

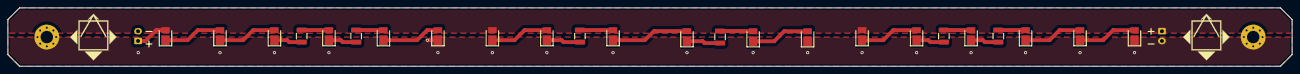
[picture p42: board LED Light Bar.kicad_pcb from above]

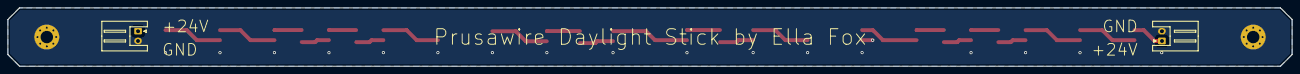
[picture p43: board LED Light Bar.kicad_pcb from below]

Board: 2 copper layers, 330.0 x 15.0 mm, 30 parts (2 on the bottom side), 23 nets.

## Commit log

2025-08-21 Prusawire 2025.B1
    [BOM.ods, LED Light Bar.kicad_pcb, LED Light Bar.kicad_sch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]
2025-09-06 Update README.md (#1)
    Updated README to add link to Klipper Config page
2025-09-13 Add Anthead Toolhead Manual
    Add pdf from https://github.com/PrintersForAnts/AntHead.git
2025-09-13 Prusawire Serial Sticker Template (#2)
    * Create README.md
    * Add files via upload
    * Rename Serial Sticker/prusawire_serial_sticker_template_V2_inkscape.svg to Serial Sticker/Inkscape/prusawire_serial_sticker_template_V2_inkscape.svg
    * Create Del
    * Delete Serial Sticker/Affinity Designer 2/Del
    * Add files via upload
    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
    [serial_sticker_cutting_stencil_V2.step, serial_sticker_cutting_stencil_V2.stl]
2025-09-16 Initial documentation of the gantry deracking process. (#4)
    * Initial documentation of the gantry deracking process.
    * Typo.
2025-09-17 Formatting fixes for Gantry Deracking doc (#5)
    * Fixed formatting.
    * Added alt-text.
    * Formating tweaks++
    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
2025-09-19 XZ Belt Install and Tensioning Documentation (#6)
    * XZ Belt Installation and Tensioning
    * Tweaks.
    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
2025-11-02 Fixed a typo and updated Mods list.
    [motor_mounts_10mm_320mm.f3d, motor_mounts_10mm_320mm.step, motor_mounts_10mm_325mm.f3d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]
2025-11-02 Added XZ Belt Reroute mod + TPU Feet
2025-11-12 First attempt at tweaks to y_belt_tensioner. tensioner_front has recess for socket cap to allow for 5-6mm of adjustment as well as R1 embossed text. tensioner_rear in both V0SN and M3S nut versions (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
    [y_belt_tensioner_front.f3d, y_belt_tensioner_front.step, y_belt_tensioner_front.stl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]
2025-11-16 Remove old rear tensioner STL.
    [y_belt_tensioner_rear.stl]
2026-02-17 Enhance tuning calibration resources and guidelines
    Added resources for calibration and tuning, including links to various guides and tools. Updated the prioritization of calibration steps.
2026-05-01 ERIK FORGOT THE STLs LOL oh and also...
    Squash 55 CAD/design commits into single history checkpoint. There are a ... lot... of binary CAD files here.
    ### e7ad8cf I don't even know anymore.
    Author: erikbuild
    Date: Fri May 1 12:49:18 2026 -0400
    ### 3575dc9 Final CAD Files
    Author: Safe
    Date: Thu Apr 30 19:57:53 2026 -0400
    Added the cad and step files for prusawire. Now off to the manual phase
    Thanks to the Github limits, i was unable to push the 54 commits. so Erick, have fun with this. I wish you good luck with stopping the scope creep😉
    ### 60f926f Update Y Axis Cad
    Author: Safe
    Date: Sat Apr 25 15:55:12 2026 -0400
    Add missing Nylock nuts per Erik and his observations
    ### 432c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
    [8mm_bearing_adapter_x2.f3d, 8mm_bearing_adapter_x2.step, 8mm_bearing_adapter_x2_LM8LUU.step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]
2026-05-07 Final Cad Edits
    Added bearing pads and reworked the caps to include small sections of VHB
    Erik is a bad infuence. Dont listen to him or HartK or Chaz or Iamus or Pooh or Matt Chu or scope creep. they keep pointing out issues with models and now i need to fix them
    [Prusawire Supplemental Badge (Combined).step, [a]_belt_clip_x4.f3d, [a]_belt_tensioner_retainers.step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]
2026-05-08 Minor fix to supports for xz_end_clips. This is entirely the fault of MakerPhil.
    [[a]_xz_end_clips.step, [a]_xz_end_clips.stl]
2026-05-09 commit 0199b2c0275c2a37f9fcd3e9ef5f8c06d02c5cbc Author: Safe Date: Sat May 9 11:21:24 2026 -0400
    The Final Final Cad
    Based on the previous modifications, the final cad has been updated
    commit e7e7080ab59a8c9a549bd24cfe83959b676c96fb
    Date: Sat May 9 11:19:57 2026 -0400
    More Final Cad Fixes
    Thanks to the work of Nexus, Erik, Downunder Maker/Phil, and our favorite project manager, Scope Creep, more files have been modified
    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
    [[a]_xz_blocks_M3Sx16T.stl, [a]_xz_blocks_M3Sx20T.stl, [a]_xz_blocks_V0Sx16T.step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]
2026-05-11 Author: Safe Date: Sun May 10 22:21:00 2026 -0400
    Updates to Bearing Fitment
    Thanks to Nexus, some issues needed fixed meaning the previous version of the cad needed to be updated.
    [8mm_bearing_adapter_x2_LM8LUU.step, 8mm_bearing_adapter_x2_LM8LUU.stl, 8mm_bearing_adapter_x2_LM8UU.step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]
2026-05-15 commit 3cf6c82ec7c801166356d2831ac792b70d7245c1 (HEAD -> main) Author: Safe <169000330+Safe-ty@users.noreply.github.com> Date: Thu May 14 22:23:12 2026 -0400
    Add Finishing Touches
    readded some missing features
    Thanks to the observations of Nomad, we needed more memes to the final cad.
    Co-Authored-By: Erik Reynolds <23739+erikbuild@users.noreply.github.com>
    commit 994fc2581d3f23930caecc61cd797f68a1f8ef8e
    Author: Safe <169000330+Safe-ty@users.noreply.github.com>
    Date: Thu May 14 19:42:57 2026 -0400
    Final Cad
    This should be the final version for the Prusawire CAD!
    Hopefully
    This
    Is
    The
    End
    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
    [[a]_xz_blocks_M3Sx16T.stl, [a]_xz_blocks_M3Sx20T.stl, [a]_xz_blocks_V0Sx16T.step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]
2026-05-16 ... whoops
    [lcd_cover_mk3_single_color.stl]
2026-05-25 commit 0fb8c268dcefaa50c8ef9c5413df01f0ae00ec30 (HEAD, main) Author: Safe <169000330+Safe-ty@users.noreply.github.com> Date: Sun May 24 11:48:57 2026 -0400
    The Final CAD V67
    Is this the final cad? only fried of the project clee knows
    commit ed4346c117acda4473f67b3e5d6df8433b846215
    Date: Sun May 24 11:47:49 2026 -0400
    Double Shear for Prusawire
    Per Alchemist's insistance, designs have been created for adding double shear using the stock motors. use F695 bearings as the secondary bearing.
    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
    [Double Shear Assembly.step, STDx10mmx341mmx20T.step, STDx8mmx320mmx16T.step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]
2026-06-05 Reorganize Double Shear and Y_Axis files into motor/variant subfolders
    why does Safe use windows if not to make my life more difficult.
    [Double Shear Assembly.step, STDx10mmx341mmx20T.step, STDx8mmx320mmx16T.step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]
2026-06-05 commit 496faa4c0122f9d3e5722a3c19a27d08cf0fab16 (HEAD -> main) Author: Safe <169000330+Safe-ty@users.noreply.github.com> Date: Thu Jun 4 10:46:08 2026 -0400
    Fix Residual Belt Issues
    Thanks to Erik Build and Scope Creep, the cad has been updated to include toothed belts in cad.
    commit cf14391fe3bc0f0b0e8b55eac56a32a0837a6e23
    Date: Wed Jun 3 22:18:41 2026 -0400
    Add more Files for Erik. 😉 😆
    commit 01828e057ea582c8e7e3ae0de9f11948b97d5d12
    Date: Wed Jun 3 22:07:55 2026 -0400
    Y Axis Rework
    Thanks to Scope Creep and Erik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
    [8mm_bearing_adapter_x2_LM8LUU.step, 8mm_bearing_adapter_x2_LM8UU.step, ADXL_Bed_Mount_Square_Expansion_Joints.step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]
2026-06-06 Author: Safe <169000330+Safe-ty@users.noreply.github.com> Date: Fri Jun 5 22:40:31 2026 -0400
    More Yaxis Updates
    Thanks for the request Nexus. Good thing Erik needs to reprocess the files 😆
    [y_belt_tensioner_Bearing_Clips_M3S_16T.stl, y_belt_tensioner_Bearing_Clips_M3S_20T.stl, y_belt_tensioner_Bearing_Clips_V0S_16T.stl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]
2026-06-15 BOM tweaks from the one true @joescalon
